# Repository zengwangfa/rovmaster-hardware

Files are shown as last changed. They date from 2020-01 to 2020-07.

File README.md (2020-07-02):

<div align="center">
  
  <a href="https://github.com/ROV-Master/rovmaster-hardware"><h1>ROV-Master</h2></a>
</div>

<div align="center">
  
  
  
</div>

## 1.ROV Master 硬件说明:pencil2:

> 电源供电为DC300V，主板基于NanoPi NEO Core，外部扩展PWM、ADC，采用电力载波/光纤与[地面站](https://github.com/ROV-Master/rovmaster-hardware)进行通信.

| 序号 | 文件夹名 | 用途 |
| :---: | :---: | :---: |
| 1 | [ROV Master Interface Board](https://github.com/ROV-Master/rovmaster-hardware/tree/master/1.ROV%20Master%20Interface%20Board%20%20V2.0) | 接线板，插入主板，用于给PWM设备信号线接入 |
| 2 | [ROV Master Mainboard](https://github.com/ROV-Master/rovmaster-hardware/tree/master/2.ROV%20Master%20Mainboard%20V3.0) | 主板，主控 |
| 3 | [ROV Master Powerboard](https://github.com/ROV-Master/rovmaster-hardware/tree/master/3.ROV%20Master%20%20Powerboard%20%20V1.0) | 舱内电源板，为设备提供1500W电源输出 |
| 4 | [ROV Master Ground Station](https://github.com/ROV-Master/rovmaster-hardware/tree/master/4.ROV%20Master%20Ground%20Station%20V1.0) | 地面站，提供通信转接及高压直流电源 |
| 5 | [ROV Master Zoom Controller](https://github.com/ROV-Master/rovmaster-hardware/tree/master/5.ROV%20Master%20Zoom%20Controller%20V3.0) | 变焦镜头控制板 |
| 6 | MP1584 VRM（Voltage Regulator Module） | 低压电源模块，4.5~28V输入，峰值3A，额定1.5A |
| 7 | [lib](https://github.com/ROV-Master/rovmaster-hardware/tree/master/lib) | Altium Designer 封装库 |

舱内装配图

## 2.ROV Master 硬件进展:family:

- [x] 舱内电路设计
	- [x] 接线板 by [@Ian](https://github.com/zengwangfa)
	- [x] ROV Master主板 by [@Ian](https://github.com/zengwangfa)	
	- [x] 舱内电源板 by [@Hyf](https://github.com/Hyf338)
- [x] 地面站 by [@Ian](https://github.com/zengwangfa)	

---

- [ ] 配件
	- [x] 变焦镜头控制板 by [@Ian](https://github.com/zengwangfa)	
	- [x] 深度传感器
		- [x] MS5837 I2C版本 by [@Ian](https://github.com/zengwangfa)	
		- [x] SPL1301 I2C版本 by [@Ian](https://github.com/zengwangfa)		 
	- [ ] MS5837 UART自带解算版本
	- [ ] 电调
		- [ ] 单向电调
		- [ ] 双向电调
	- [ ] 9轴模块
	- [ ] 水下监控摄像头
	- [ ] 探照灯
	- [ ] 舵机调试器	
	- [x] DC-DC 24V/3A 降压模块

#### Github下载过慢
- [Github下载过慢解决办法](https://blog.csdn.net/wangshuaiwsws95/article/details/104730741/)
	
#### 参与贡献
- Fork 本仓库
- 新建分支
- 提交
- 新建 Pull Request
- [点击联系我](Mailto:zengwangfa@outlook.com)

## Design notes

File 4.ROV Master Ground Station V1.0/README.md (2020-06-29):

<p align="center">
  
</p>

<p align="center">
  
  
</p>

# 1.新增加的特性

- 使用MT7688N模块，作为无线路由器(PC端网口、电力载波网口、光电转换网口、WiFi之间进行透传)
- 使用AC-DC隔离开关电源模块[Hi-Link 20W DC24V](https://detail.tmall.com/item.htm?id=607394173667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)对地面站设备进行供电，并在AC220V前端增加EMI滤波、保护电路
- 增加光电转换器接口
- 增加AC220电流电压表

地面站实物图

# 2.说明

- [仪表盒开孔尺寸图 文件夹](https://github.com/ROV-Master/rovmaster-hardware/tree/master/4.ROV Master Ground Station V1.0/仪表盒开孔尺寸图) 存放地面站**侧板**、上盖板开孔尺寸图

地面站内部设计连接图

# 3.后续可改进的地方
- 1.壳体上盖板电流电压表位置，开孔外扩0.5mm即可（原先为1mm）
- 2.WAN口可引出RJ45接口备用
- 3.PC端RJ45网口可挨紧

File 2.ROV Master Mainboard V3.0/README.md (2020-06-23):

<p align="center">
  
</p>

<p align="center">
  
  
</p>

# 1.新增加的特性

- 增加PWM端光耦隔离
- 电源输入为高压直流输入(DC300V)
- 稳压电源后端3.3V、5.0V增加TVS管(在稳压模块异常时保护后端电路)

# 2.说明

- `MainBoard.step`文件为PCB 3D视图文件
- `电源接口及电流采样`文件夹为之前原理图备份

# 3.后续可改进的地方

- 放置请勿触摸图标
- 增加DC310V测试点
- 蜂鸣器`BEEP(C0)`引脚加一个1K下拉引脚
- 地之间隔离的磁珠可以并联一个103电容(用于吸收杂波)
- TVS管标称电压(VRWM)应略大于工作电压，TVS的钳制电压(VCL)尽量大

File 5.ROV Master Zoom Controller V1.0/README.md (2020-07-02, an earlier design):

<p align="center">
  
</p>

<p align="center">
  
  
</p>

# 1.新增加的特性

- 使用`MCU` STM32F103C8T6 
- 增加`CP2102`  USB转UART模块进行调试
- 使用A4988步进电机驱动模块

# 2.说明

[A4988 文件夹](https://github.com/ROV-Master/rovmaster-hardware/tree/master/5.ROV Master Zoom Controller V1.0/A4899) 存放A4988步进电机驱动芯片datasheet、尺寸图

# 3.后续改进的地方

### 3.1 设计缺陷
- A4988驱动器为驱动8~35V步进电机，若为低压步进电机可以使用[DRV8834驱动模块](https://www.pololu.com/product/2134) 

A4988步进电机励磁序列

变焦镜头步进电机励磁序列

| STEP |  1 |  22  |  33  |  4 |
| :--: | :--: | :--: | :--: | :--: |
|  A+  |  1 |  1 |  0 |  0 |
|  A-  |  1 |  0 |  0 |  1 |
|  B+  |  0 |  0 |  1 |  1 |
|  B-  |  0 |  1 |  1 |  0 |

- 由上图可知，但是由于变焦镜头步进电机节拍表与普通的并不一致，因此此类型的驱动模块并不适用

### 3.2 解决方案
- 因而需要使用最原有方案，利用达林顿管芯片进行驱动(eg.ULN2803、ULN2003驱动芯片)
- ULN2003为7通道达林顿管，但是变焦镜头有2个4相步进电机，因此使用ULN2803驱动芯片（8通道）

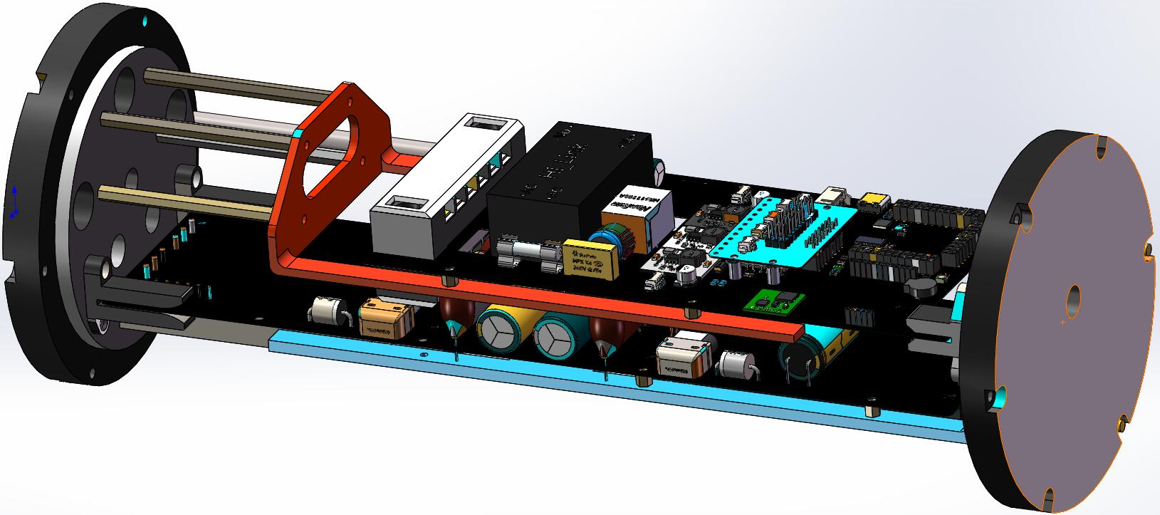
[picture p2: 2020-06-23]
doc/pictures/Chamber_structure1.jpg

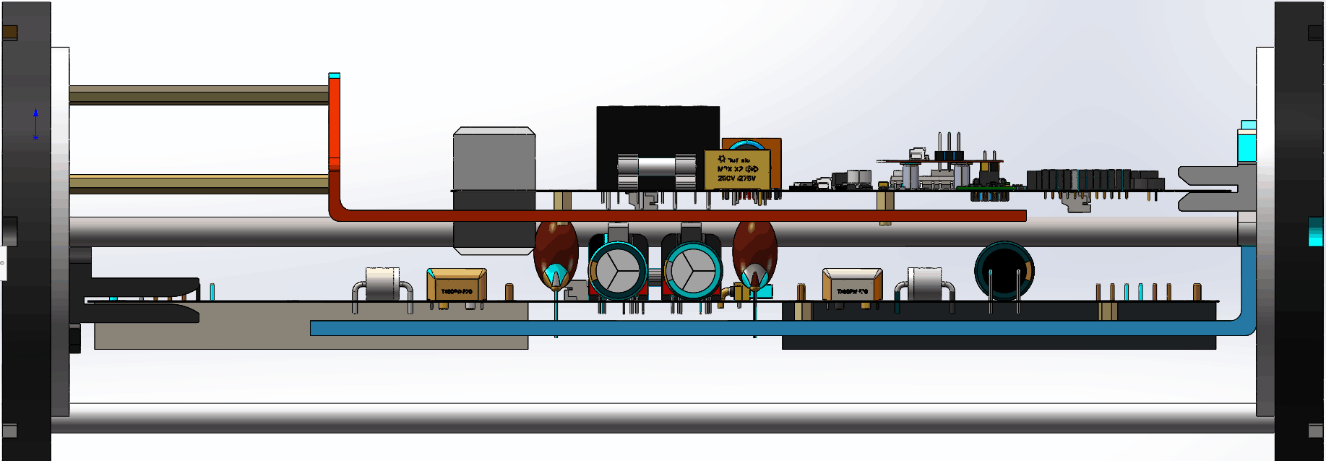
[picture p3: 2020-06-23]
doc/pictures/Chamber_structure2.png

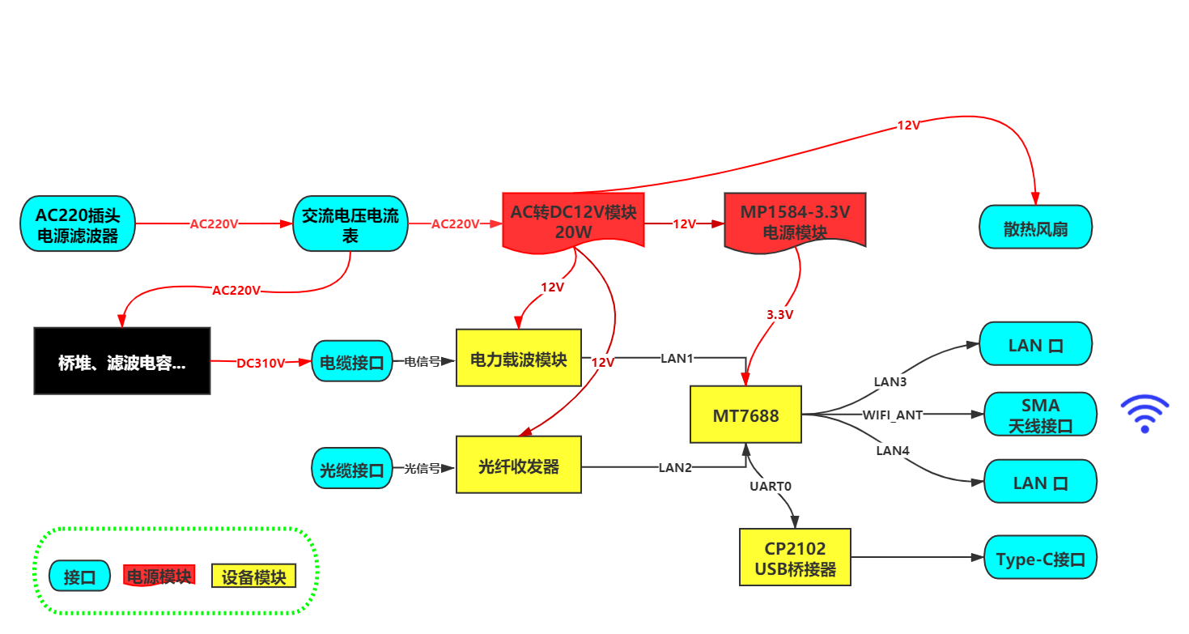
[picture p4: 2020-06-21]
4.ROV Master Ground Station V1.0/Ground_Station_Structrue.png

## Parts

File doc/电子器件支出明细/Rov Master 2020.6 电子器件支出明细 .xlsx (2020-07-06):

ROV 电子器件支出明细表
器材名称 | 数量 | 总价 | 日期 | 是否有发票
捷配 第一代主板PCB | 5 | 108 |  | 1电子发票
220V转24V20W稳压隔离电源模块 (https://detail.tmall.com/item.htm?id=607394173667&_u=k1v2ldgsf448&skuId=4432714442007) | 4 | 94 | 6.11 | 电子发票
PCB板清洗剂除胶除尘 (https://item.taobao.com/item.htm?spm=a1z09.2.0.0.2d1f2e8do3zeDh&id=9893313086&_u=k1v2ldgsa688) | 1 | 17 | 6.12
大功率二极管30A10单向导通 (https://item.taobao.com/item.htm?spm=a1z09.2.0.0.2d1f2e8do3zeDh&id=581965527987&_u=k1v2ldgse40c) | 10 | 21.8 | 6.12
定制XT60/XT30电源线 (https://detail.tmall.com/item.htm?id=15100319583&spm=a1z09.2.0.0.2d1f2e8do3zeDh&_u=k1v2ldgs5d34) | 10/5 | 180 | 6.13 | 1
TB1506接线端子/6位短路片 (https://detail.tmall.com/item.htm?id=610080819934&spm=a1z09.2.0.0.2d1f2e8do3zeDh&_u=k1v2ldgsf44b) | 10 | 32.79 | 6.13
XT30接头/电源硅胶线 (https://detail.tmall.com/item.htm?id=559203984858&spm=a1z09.2.0.0.2d1f2e8do3zeDh&_u=k1v2ldgscda4) | 5 | 36.65 | 6.13
芯片主板元器件散热片 (https://item.taobao.com/item.htm?spm=a1z09.2.0.0.2d1f2e8do3zeDh&id=602118161849&_u=k1v2ldgsba53) | 5 | 7.1 | 6.13
捷配 主板/电源板PCB (https://detail.tmall.com/item.htm?id=597612948368&spm=a1z09.2.0.0.2d1f2e8do3zeDh&_u=k1v2ldgsaa5d) | 5/5 | 324 | 6.13 | 1电子发票
PCA9685芯片 (https://item.taobao.com/item.htm?spm=a1z09.2.0.0.2d1f2e8do3zeDh&id=557114520914&_u=k1v2ldgs5378) | 4 | 25.87 | 6.14
JY901B 九轴模块 (https://item.taobao.com/item.htm?spm=a1z09.2.0.0.2d1f2e8do3zeDh&id=43511899945&_u=k1v2ldgsb9b2) | 1 | 134 | 6.14 | 1
塑料盒长方形盒子工具盒 (https://detail.tmall.com/item.htm?id=581874651313&spm=a1z09.2.0.0.2d1f2e8do3zeDh&_u=k1v2ldgs4223) | 1 | 71.88 | 6.14 | 1电子发票
优信 电子元器件 (https://youxin-electronic.taobao.com/shop/view_shop.htm?user_number_id=2658592015) | 若干 | 171.8 | 6.14 | 1
贴片单排母/排针 (https://detail.tmall.com/item.htm?id=569406041078&spm=a1z09.2.0.0.2d1f2e8do3zeDh&_u=k1v2ldgs0d14) | 5 | 12.8 | 6.14
元器件收纳盒 (https://item.taobao.com/item.htm?spm=a1z09.2.0.0.2d1f2e8do3zeDh&id=43331772336&_u=k1v2ldgs6af2) | 3 | 58.82 | 6.14
220V 交流电压电流表/热缩管 (https://item.taobao.com/item.htm?spm=a1z09.2.0.0.300e2e8dPqPSZj&id=563971657103&_u=n1v2ldgsf55d) | 1/3 | 124.35 | 6.20 | 1
插座式紧凑型电源滤波器 (https://item.taobao.com/item.htm?spm=a1z09.2.0.0.300e2e8dPqPSZj&id=607137400635&_u=n1v2ldgs7cbf) | 2 | 101 | 6.20 | 1
MT7688路由器模块/稳压隔离电源 (https://detail.tmall.com/item.htm?id=597619548455&spm=a1z09.2.0.0.300e2e8dPqPSZj&_u=n1v2ldgs2484) | 2/2 | 153 | 6.20 | 1电子发票
荣新 地面站PCB/侧板PCB/侧板PCB (https://item.taobao.com/item.htm?spm=a1z09.2.0.0.300e2e8dPqPSZj&id=9379760689&_u=n1v2ldgs2b09) | 5/5/5 | 271 | 6.21 | 1电子发票
优信 电子元器件 (https://youxin-electronic.taobao.com/shop/view_shop.htm?user_number_id=2658592015) | 若干 | 221.3 | 6.21 | 1
贴片单排母/排针 (https://detail.tmall.com/item.htm?id=569406041078&spm=a1z09.2.0.0.2d1f2e8do3zeDh&_u=k1v2ldgs0d14) | 若干 | 39.8 | 6.23 | 1电子发票
A4988步进电机模块 (https://detail.tmall.com/item.htm?id=610688807041&spm=a1z09.2.0.0.300e2e8deJ7bMh&_u=n1v2ldgs5d2d) | 2 | 9.6 | 6.23
冷压插头接线端子公母快速连接器 (https://detail.tmall.com/item.htm?id=620331380782&spm=a1z09.2.0.0.977a2e8dSL2XP5&_u=t1v2ldgs7800) | 50 | 13.34 | 6.24
双头USB口数据线两头公对公 (https://buyertrade.taobao.com/trade/detail/tradeSnap.htm?tradeID=1085822114156724883&snapShot=true) | 3 | 41.53 | 6.25
全新静音风扇 2510 2.5厘米 12V (https://item.taobao.com/item.htm?spm=a1z09.2.0.0.977a2e8dSL2XP5&id=41680128557&_u=t1v2ldgs8321) | 3 | 25 | 6.27
20 AWG特软高温硅胶排线 (https://item.taobao.com/item.htm?spm=a1z09.2.0.0.977a2e8dSL2XP5&id=557843049825&_u=t1v2ldgs893e) | 3 | 22.2 | 6.27
优信 电子元器件 (https://youxin-electronic.taobao.com/shop/view_shop.htm?user_number_id=2658592015) | 若干 | 75 | 6.27 | 1
金属电缆防水接头葛兰头 (https://item.taobao.com/item.htm?spm=a1z09.2.0.0.977a2e8dSL2XP5&id=611336897072&_u=t1v2ldgsbf57) | 4 | 21.31 | 6.27
PH红白排线双头PH2.0mm端子线 (https://item.taobao.com/item.htm?spm=a1z09.2.0.0.977a2e8dSL2XP5&id=584930779544&_u=t1v2ldgs0031) | 30 | 45.4 | 6.29
优信 电子元器件 (https://youxin-electronic.taobao.com/shop/view_shop.htm?user_number_id=2658592015) | 若干 | 94.88 | 6.29 | 1
ULN2803 达林顿管 (https://detail.tmall.com/item.htm?id=41272630297&spm=a1z09.2.0.0.30552e8da7n1VT&_u=21v2ldgsc303) | 8 | 28.4 | 7.1
共计 |  | 2352.34

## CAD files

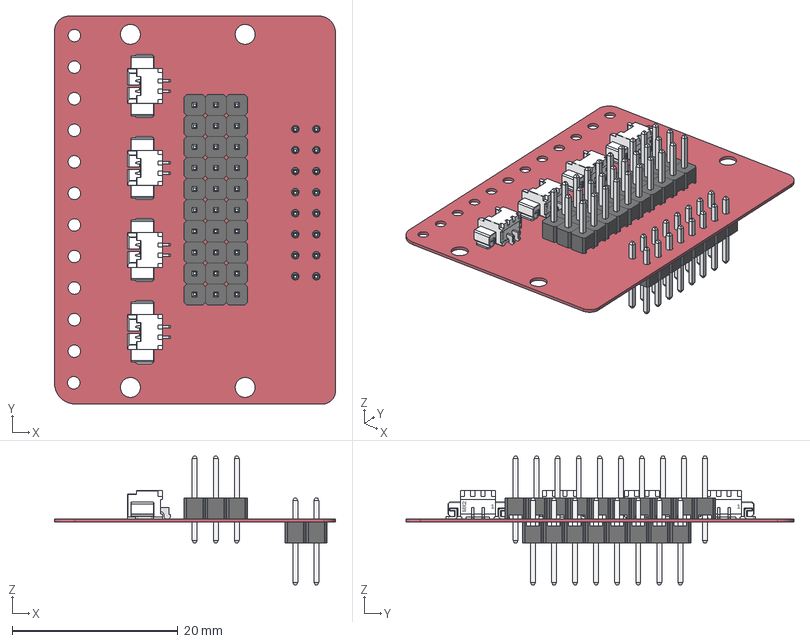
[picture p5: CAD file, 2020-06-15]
1.ROV Master Interface Board V2.0/interface.step
33.9 x 46.8 x 15.6 mm
Board
MOLEX1.25-WS-竘褐 x 8
LOGO?0.25 x 4
MOLEX1.25-WS-2P x 4
HEADER x 49

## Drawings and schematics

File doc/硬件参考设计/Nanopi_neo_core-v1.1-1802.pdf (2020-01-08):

# NanoPi NEO Core

# Revision

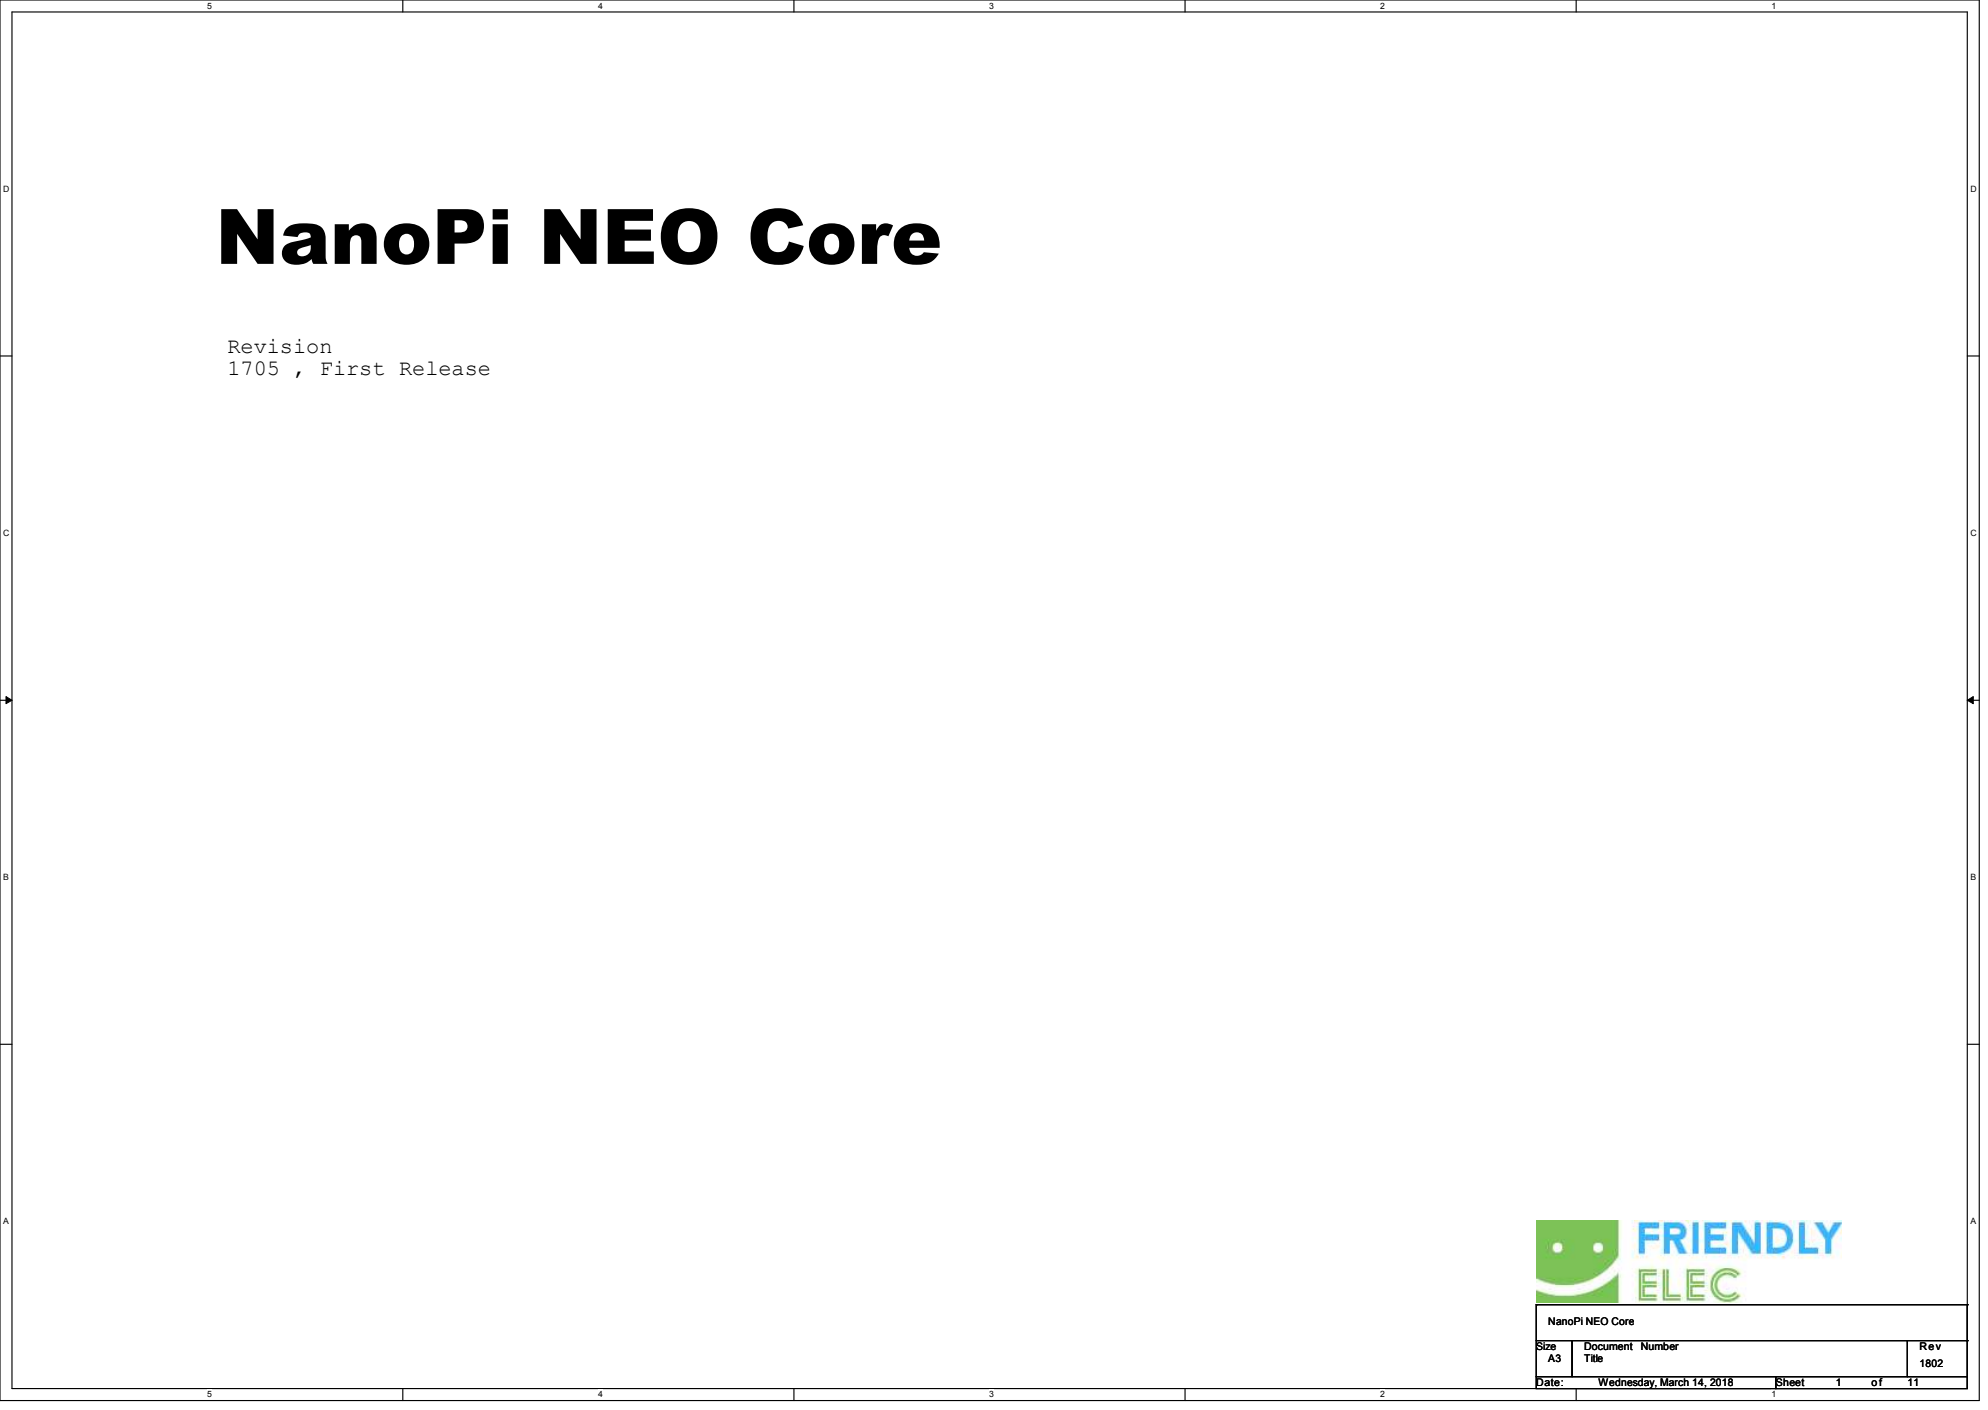
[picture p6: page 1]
1705 , First Release; Size; Document Number; Date:; Sheet; Title; Wednesday, March 14, 2018

NanoPi NEO Core

# BLOCK

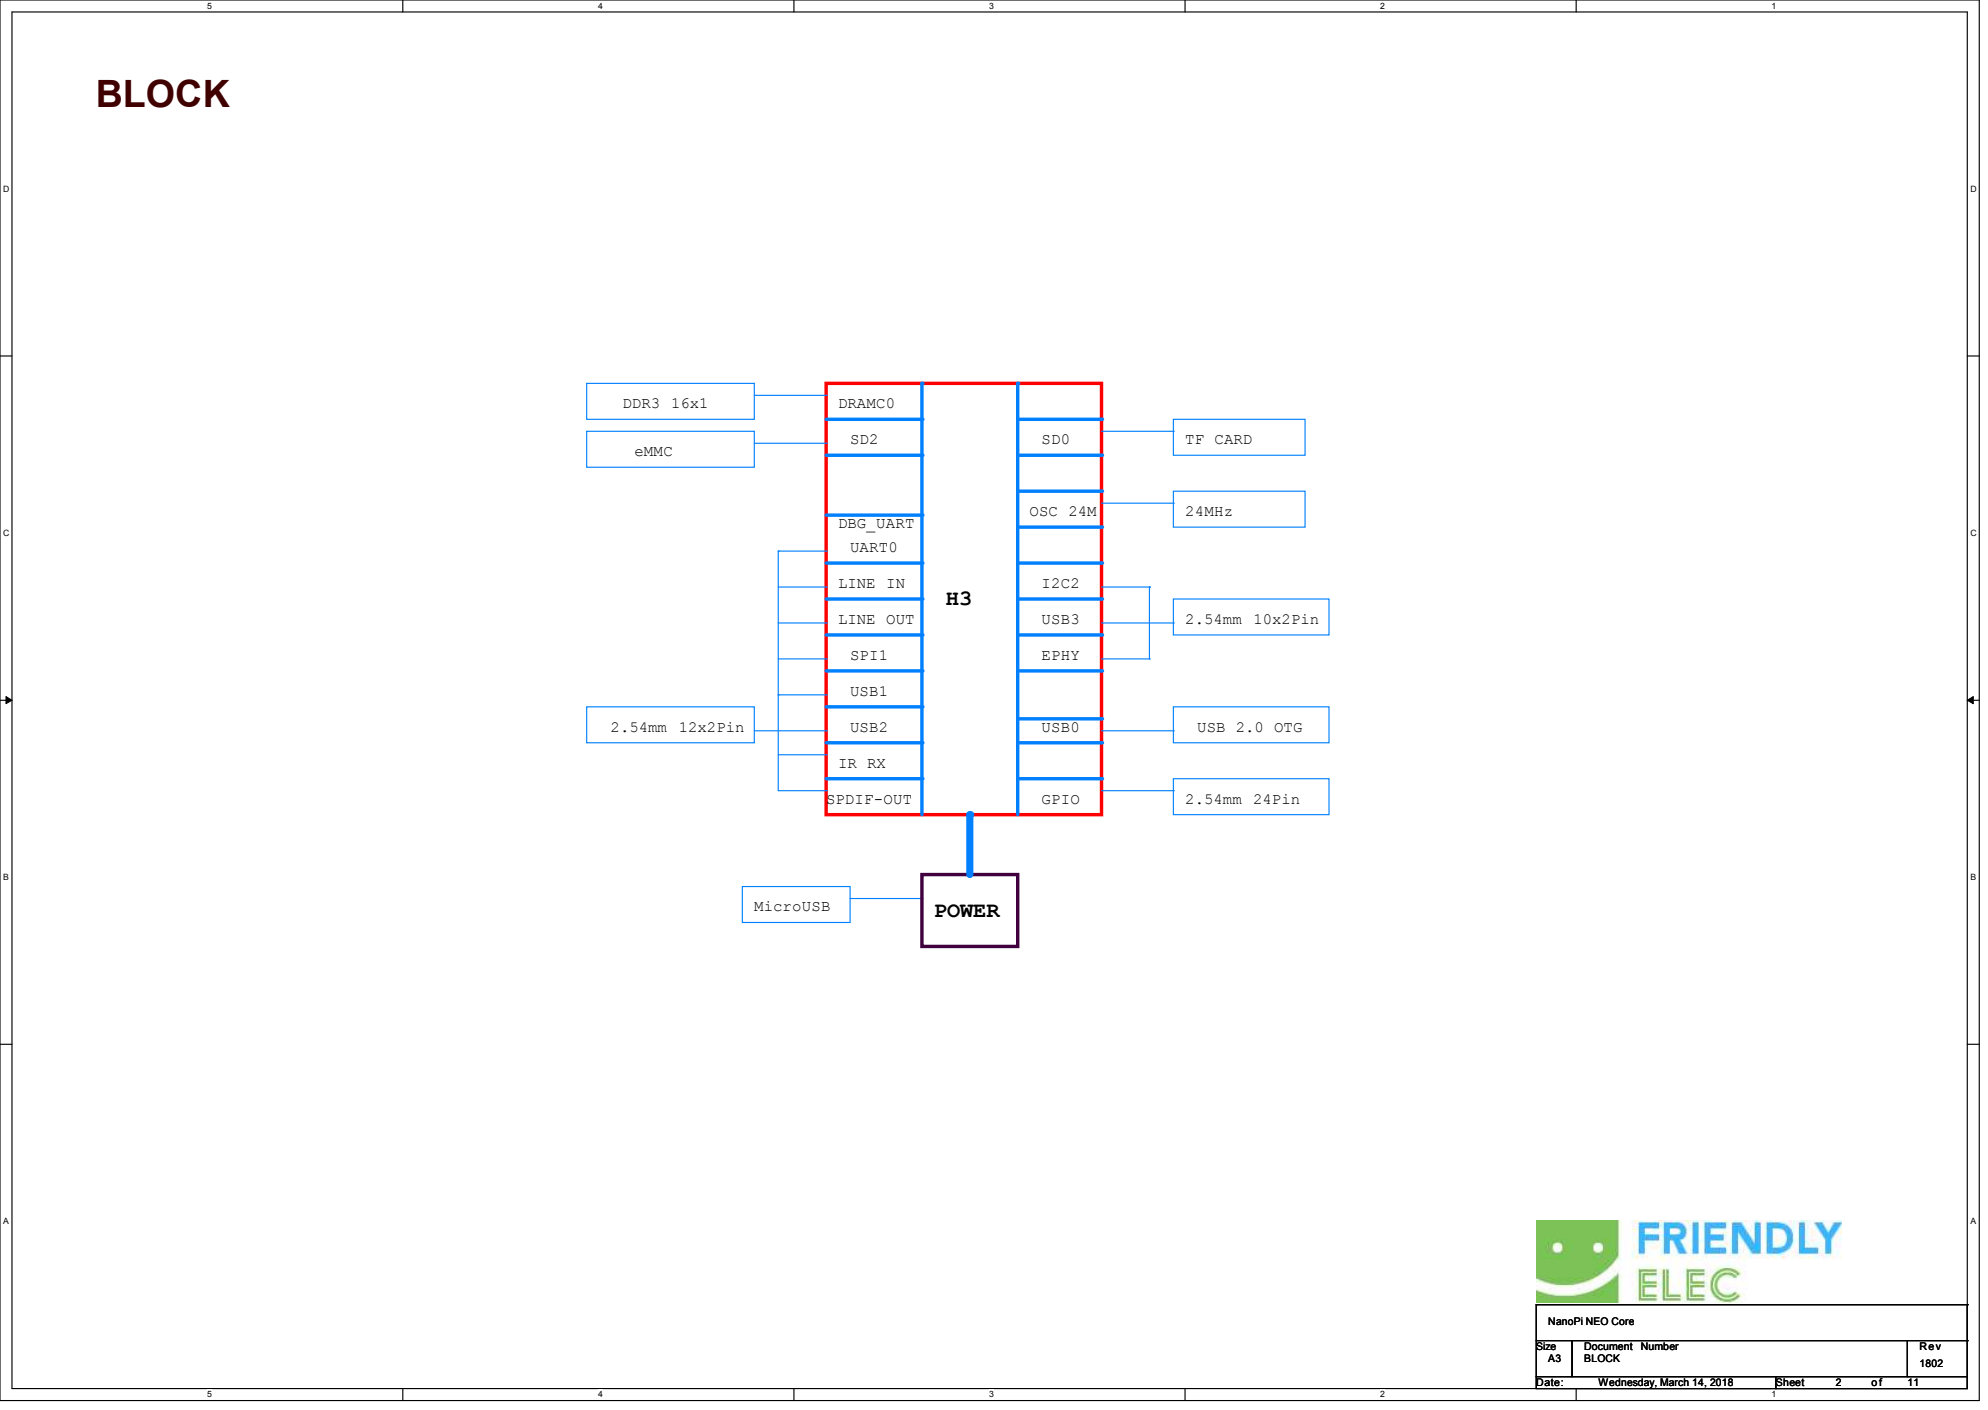
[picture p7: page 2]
TF CARD; USB0; USB1; OSC 24M; 24MHz; EPHY; MicroUSB; DDR3 16x1; DRAMC0; USB3; POWER; LINE OUT; 2.54mm 12x2Pin; USB2; USB 2.0 OTG; LINE IN; SPDIF-OUT; GPIO; 2.54mm 24Pin; UART0; DBG_UART; 2.54mm 10x2Pin; SPI1; SD2 eMMC; BLOCK; Wednesday, March 14, 2018

# POWER TREE

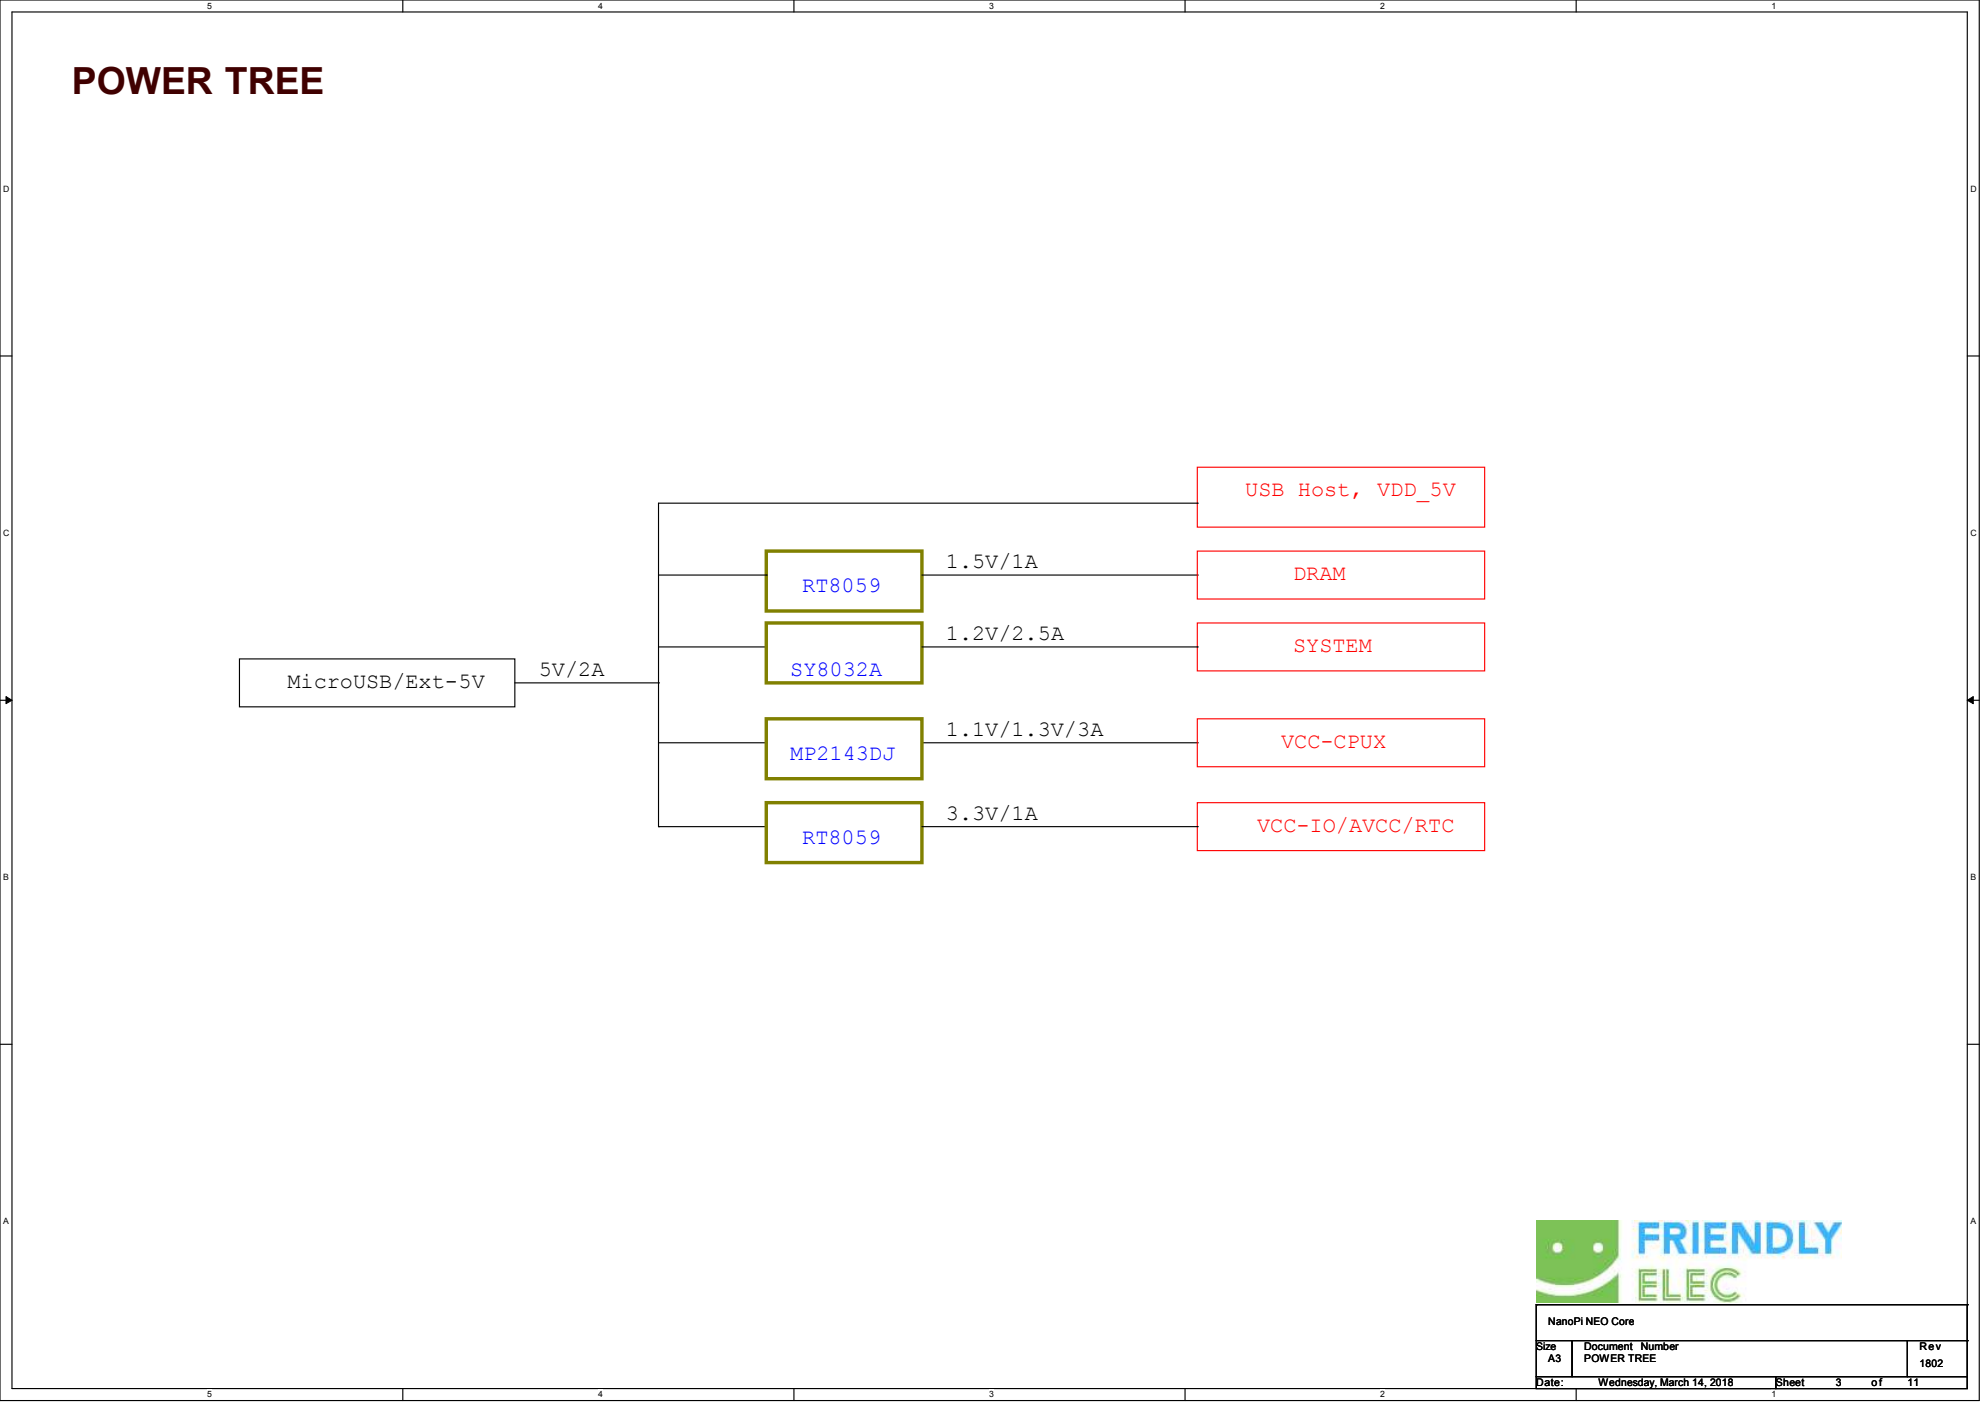
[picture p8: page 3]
MicroUSB/Ext-5V; USB Host, VDD_5V; DRAM; VCC-CPUX; SYSTEM 1.2V/2.5A; POWER TREE; Wednesday, March 14, 2018

VCC-IO/AVCC/RTC RT8059

# DDR3 16x1

# DRAM

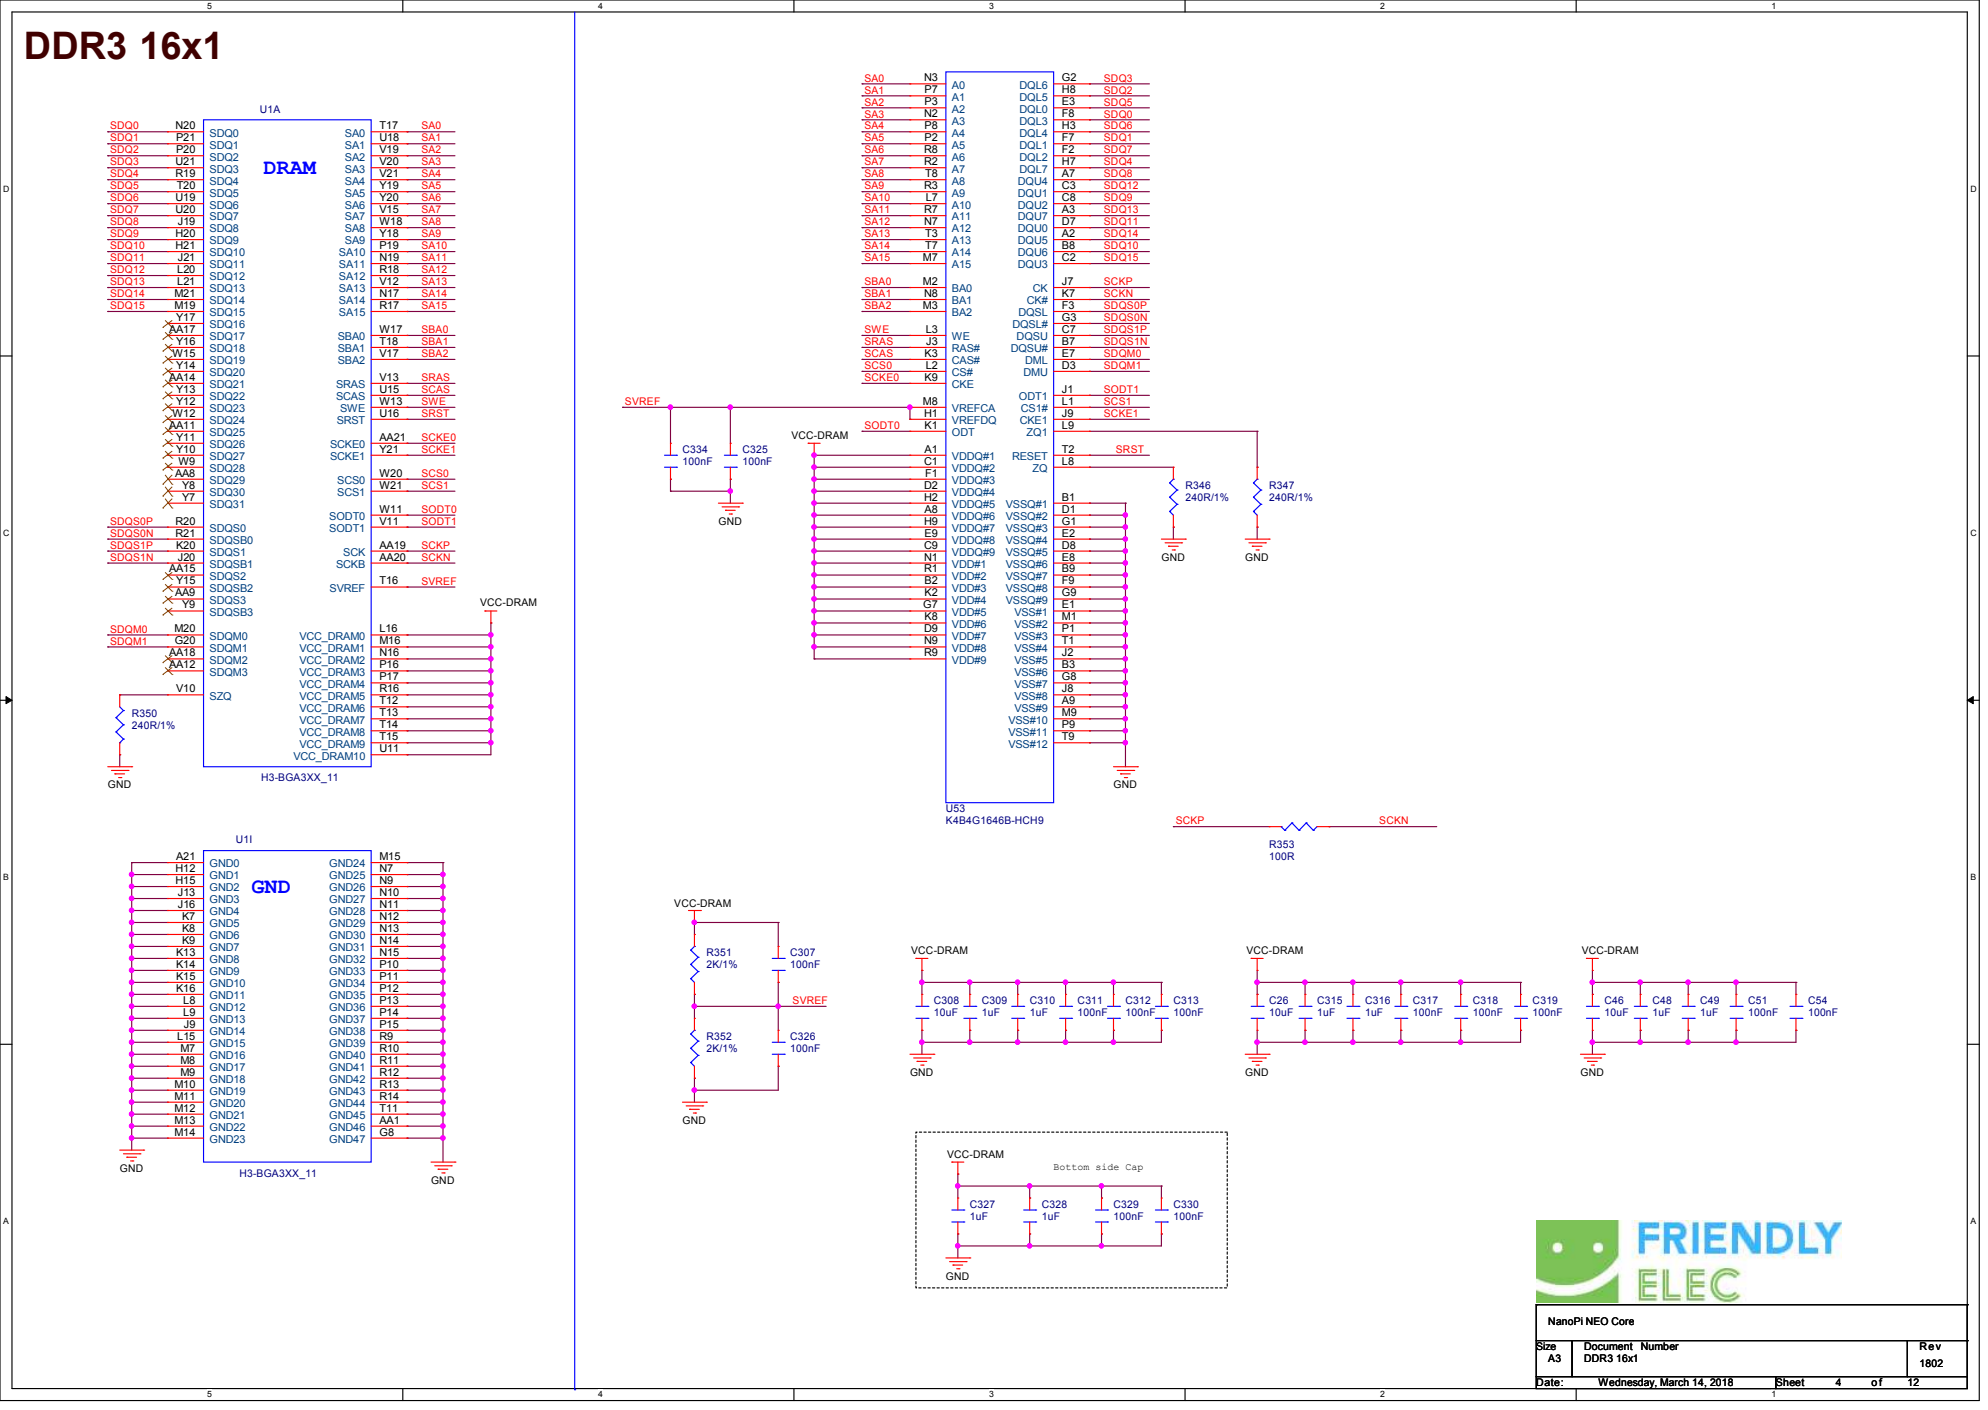
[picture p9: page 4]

# CPU 01

# SDC1

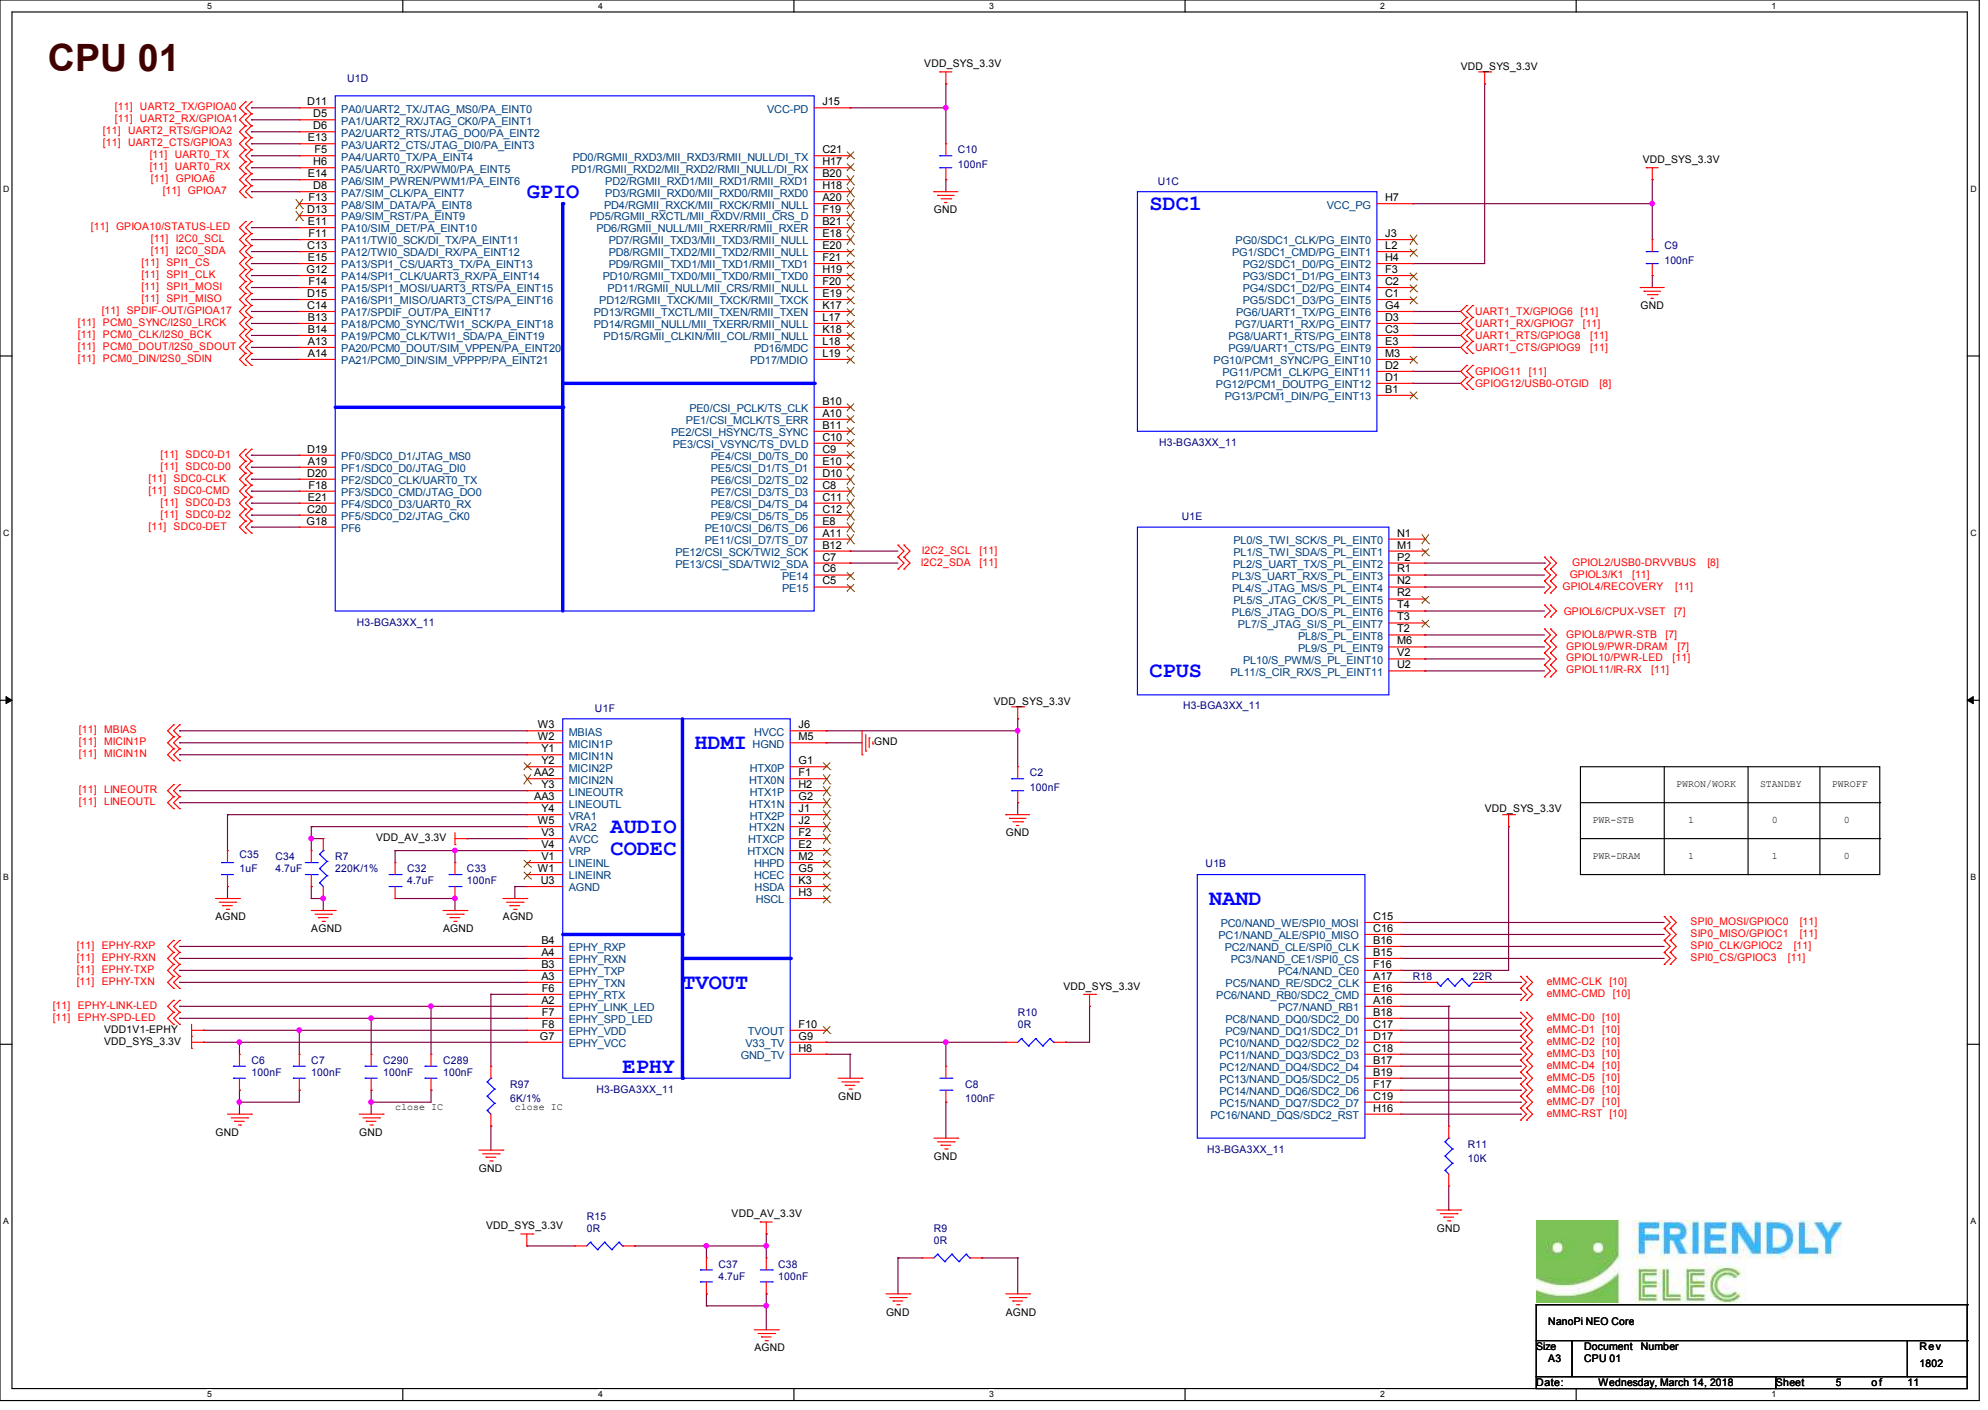
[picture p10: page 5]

# CPU 02

# USB

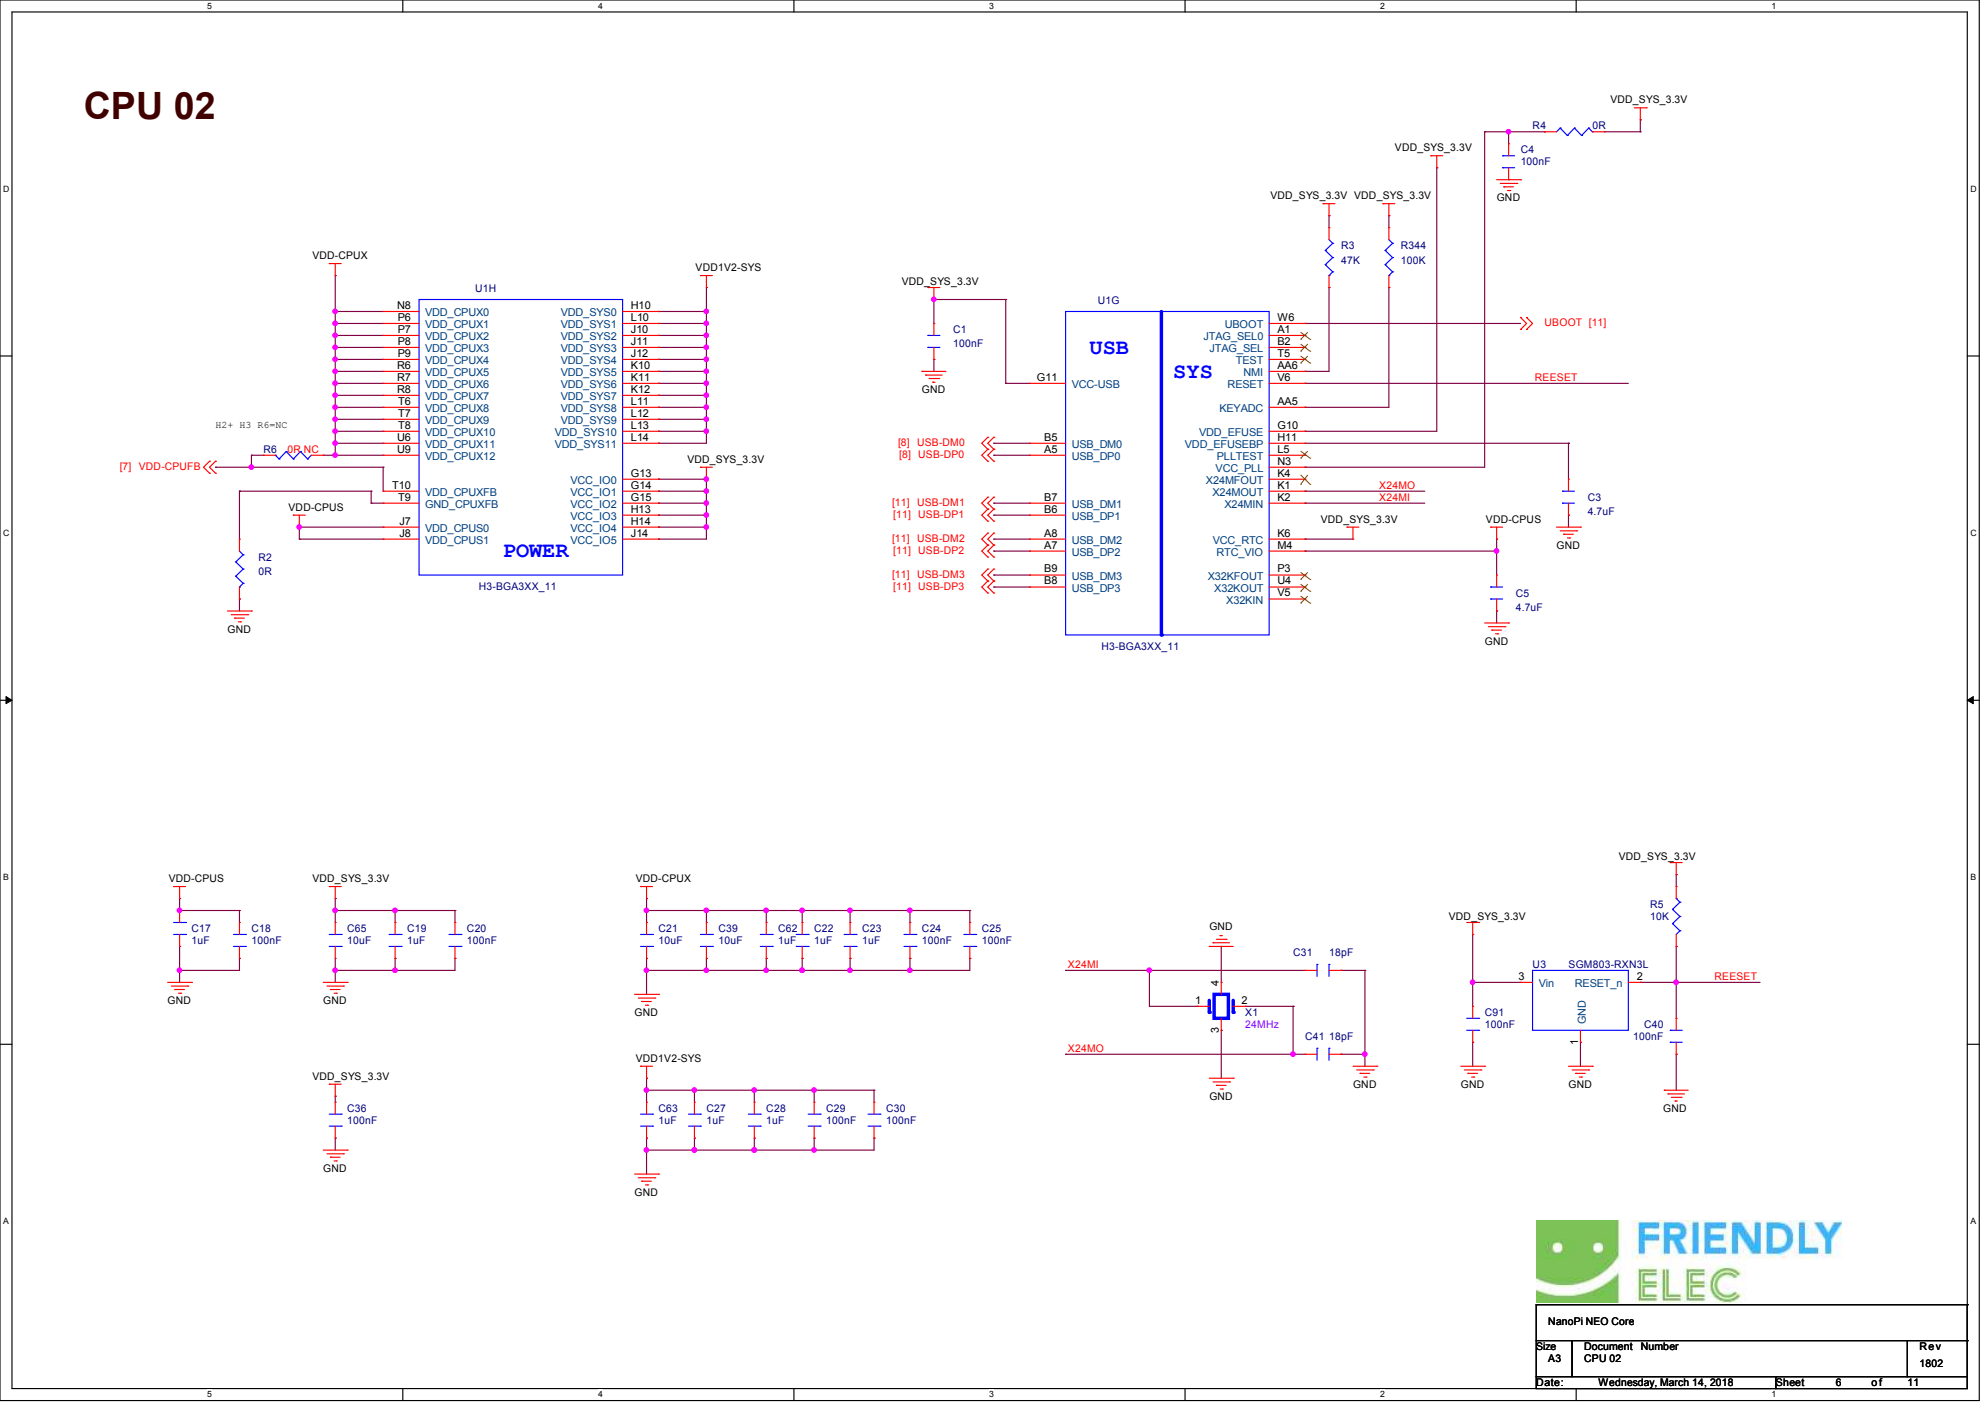
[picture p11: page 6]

# POWER 01

1.5V/1A

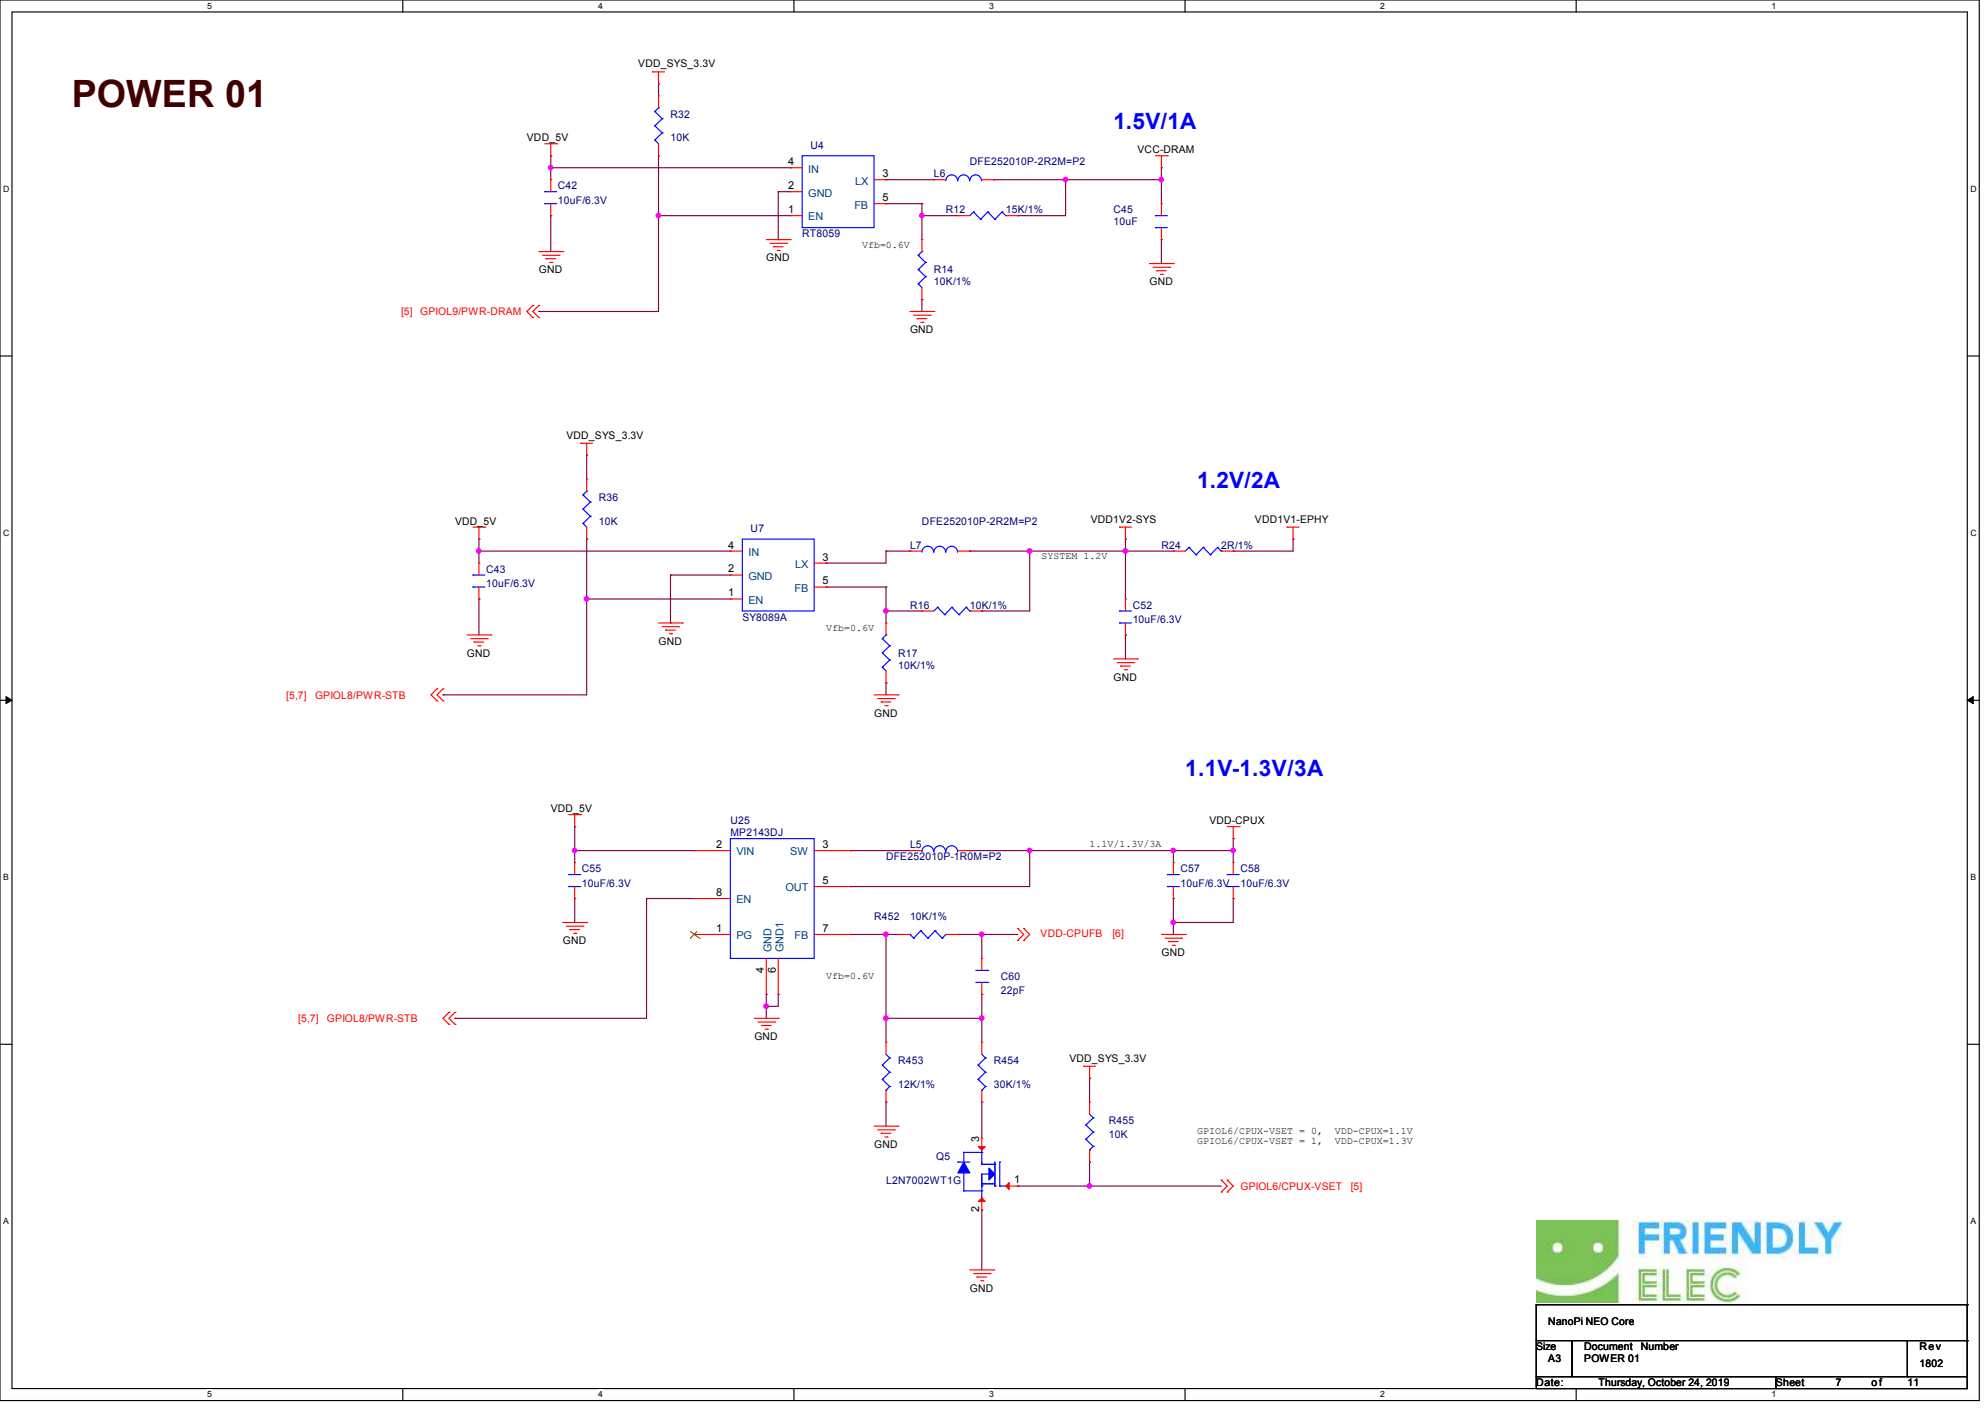
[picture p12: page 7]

D | D

# POWER 02

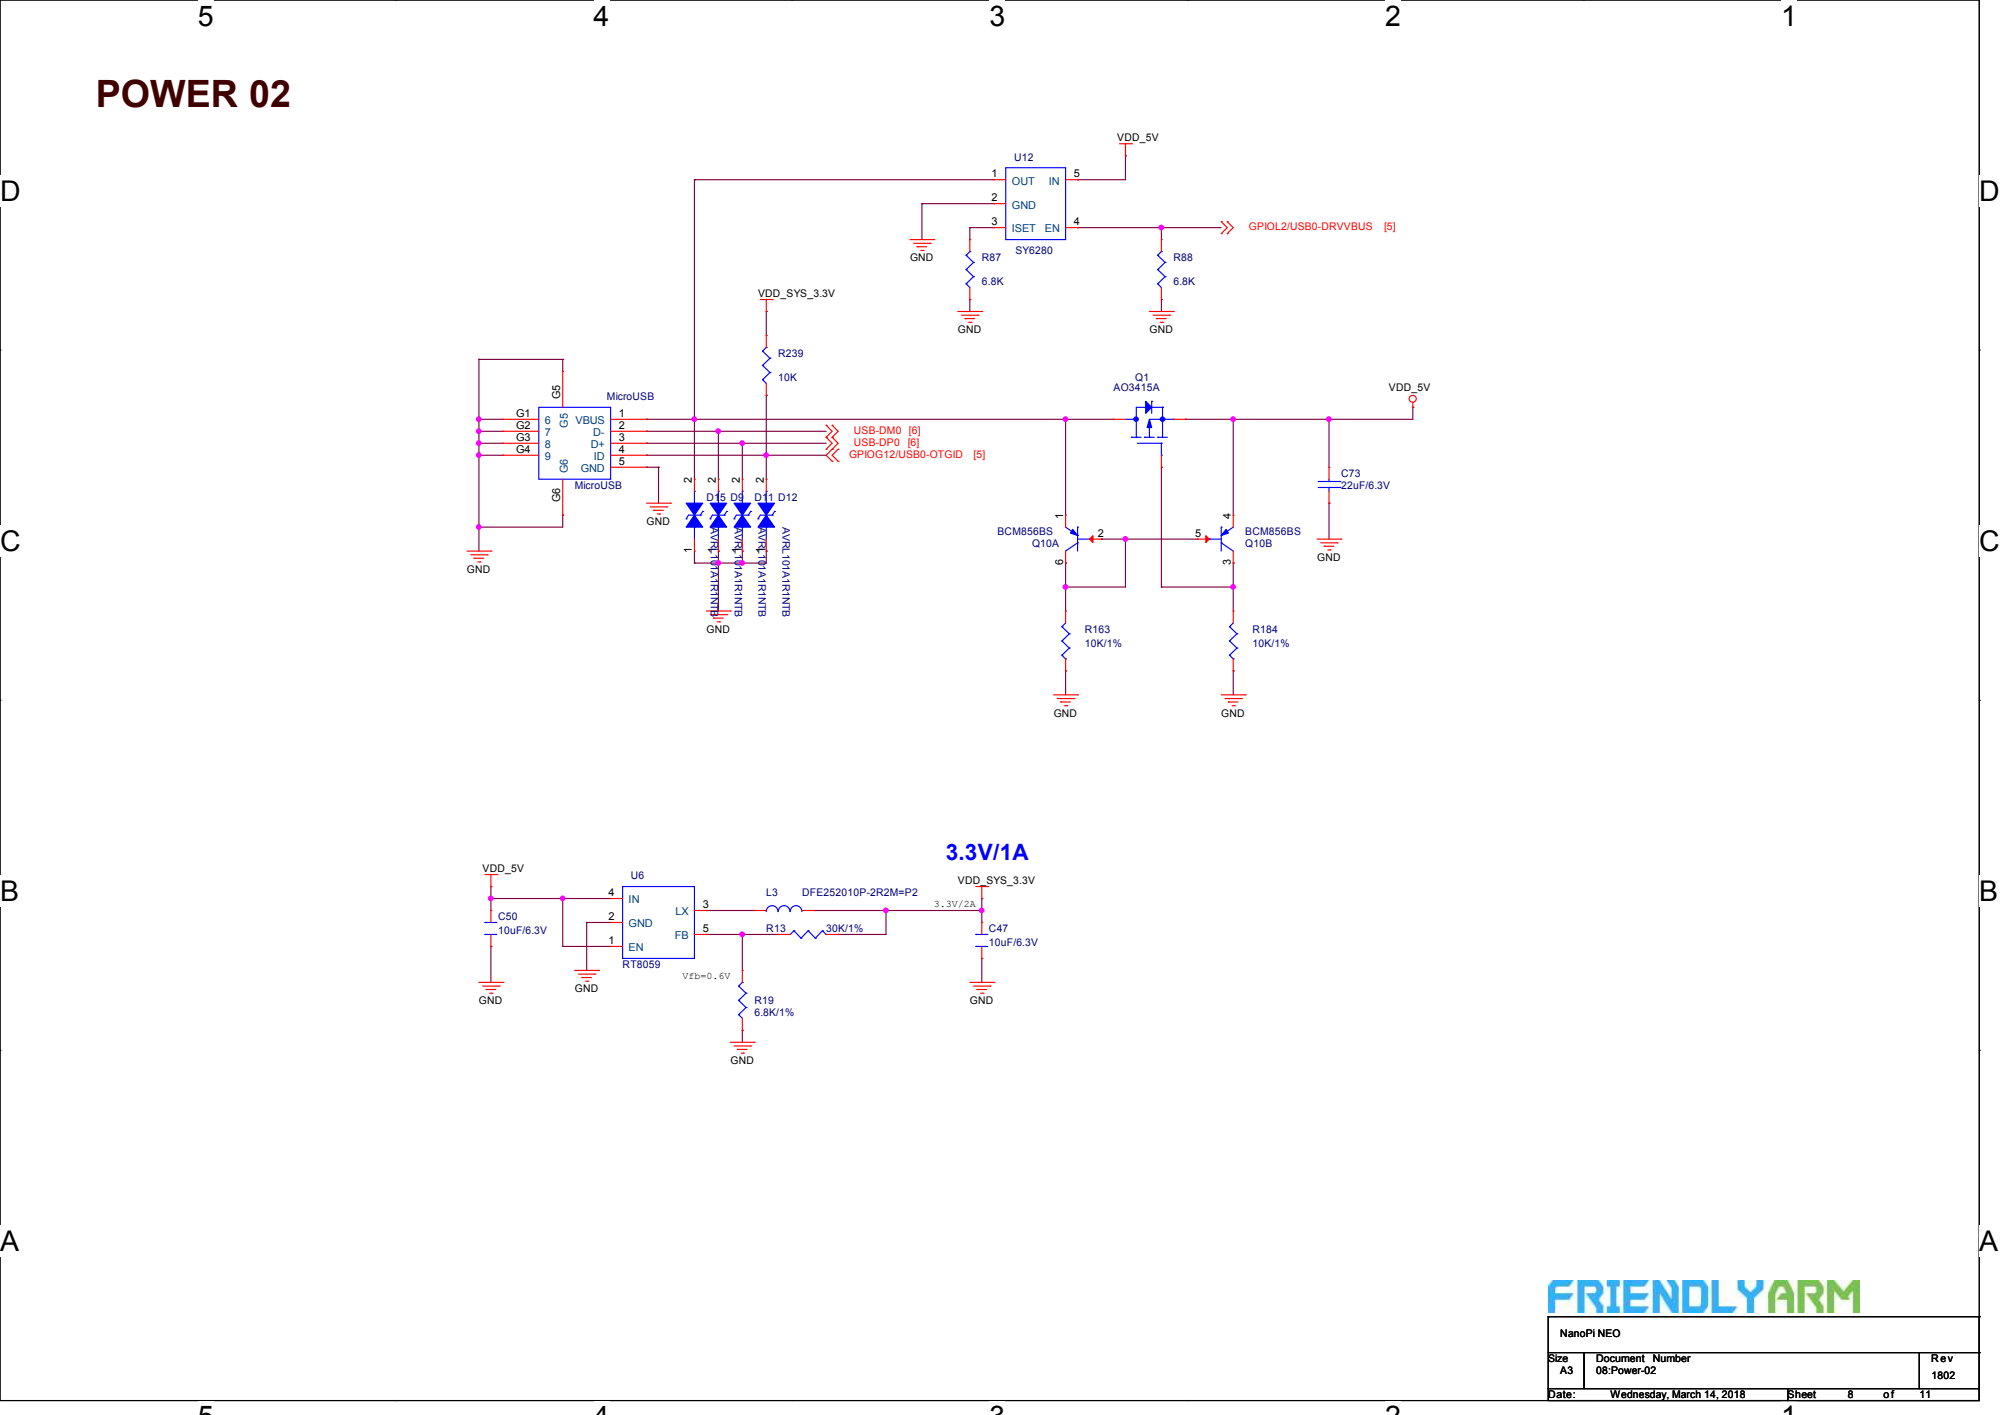
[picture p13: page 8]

# eMMC

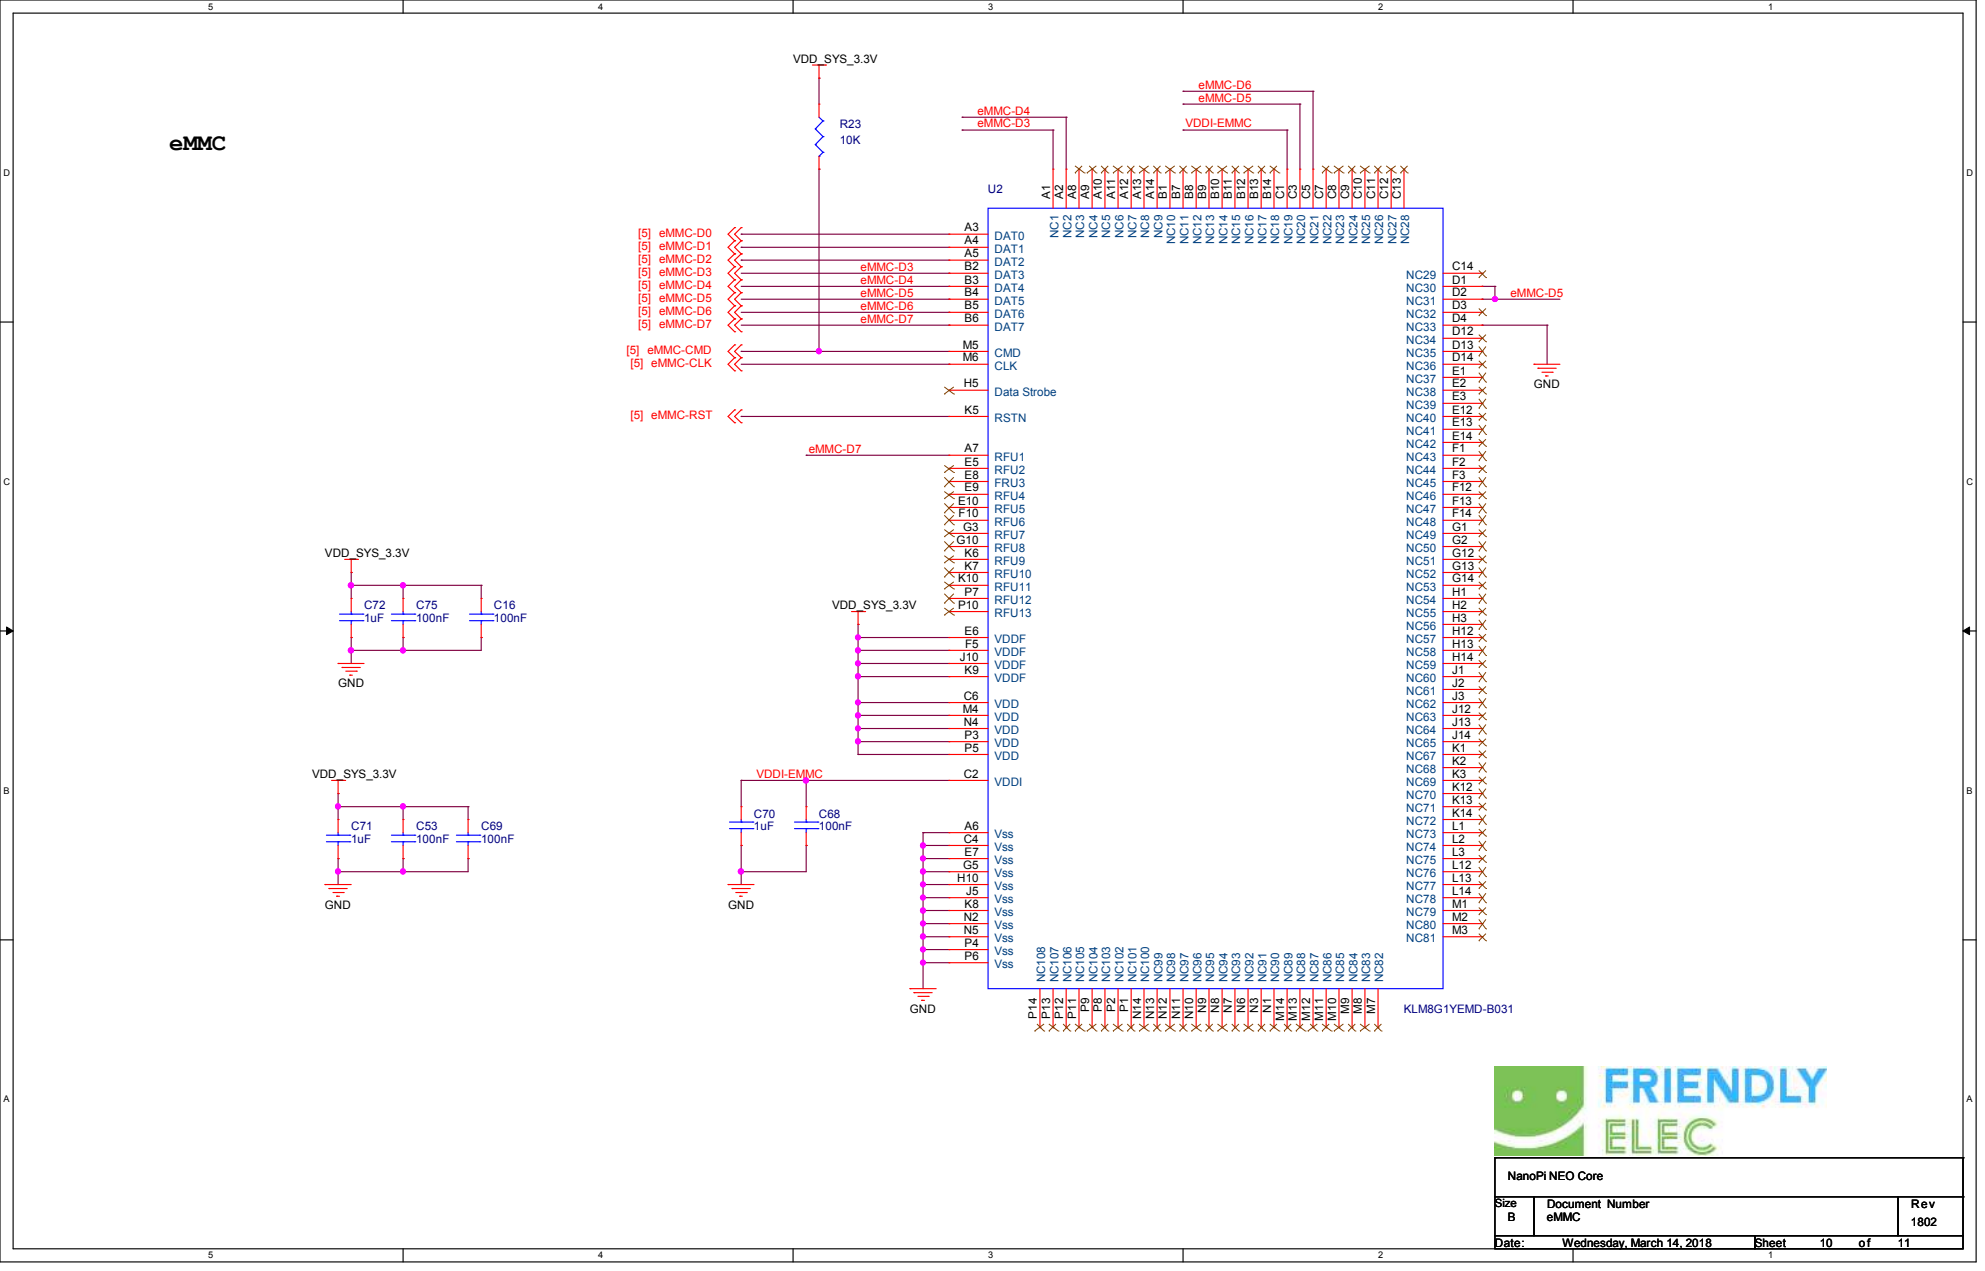
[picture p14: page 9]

# GPIO,Card,LEDs

## D4RClamp0531T/NC

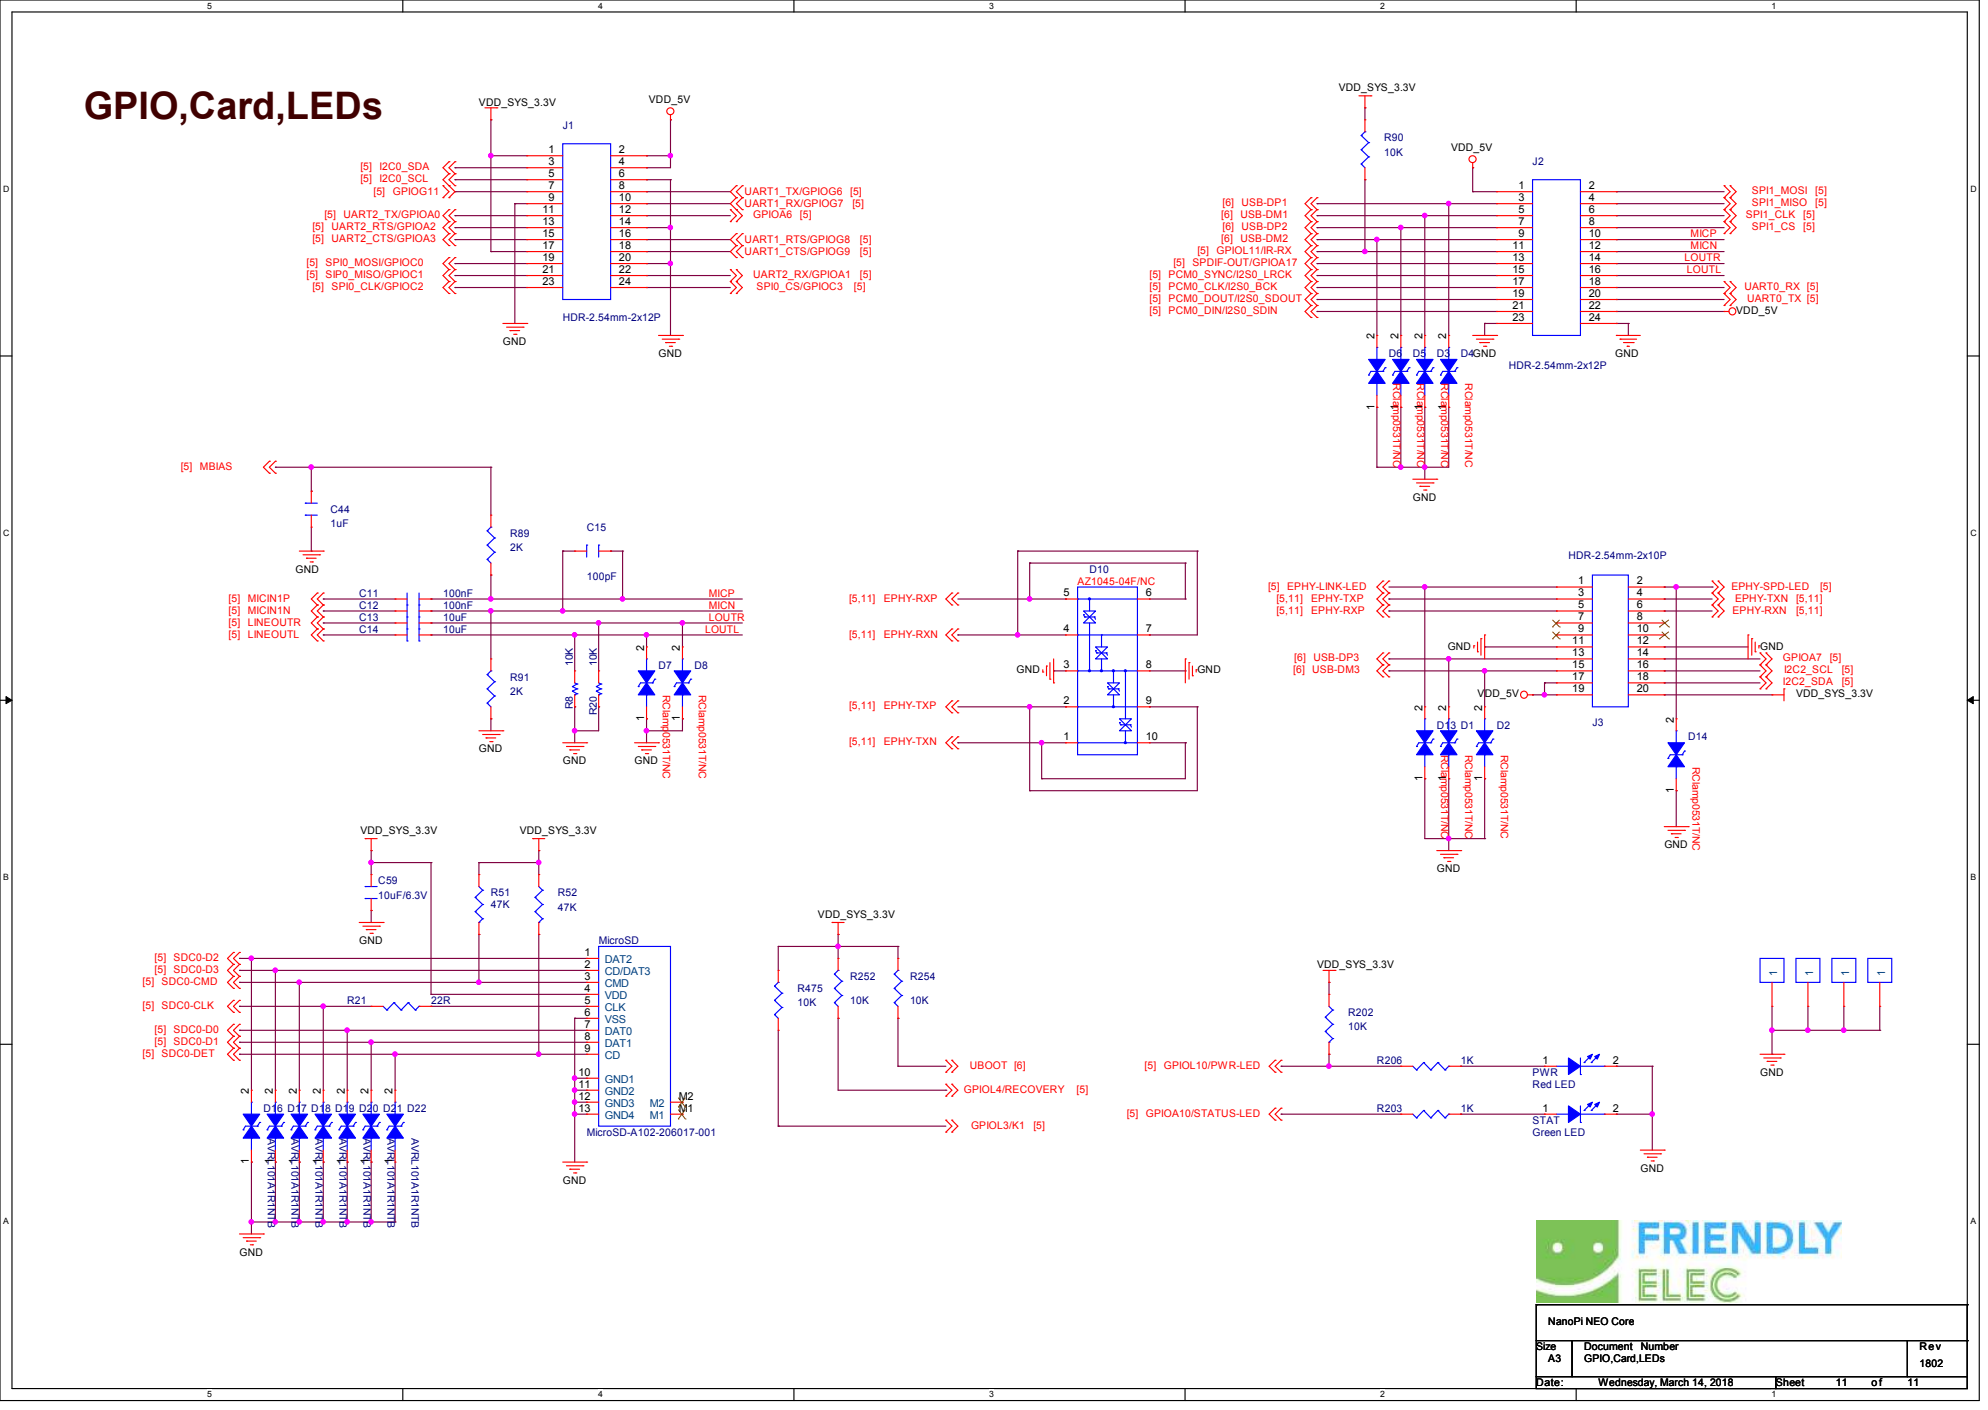
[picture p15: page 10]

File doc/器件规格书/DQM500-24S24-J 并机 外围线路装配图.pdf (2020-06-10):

一、 组装准备：

1、 将 2 只全砖模块铝板上粘贴的保护膜（黄色）全部揭掉。

2、 把模块铝板底部涂上导热硅脂，按照 S9A 型机壳内全砖位置用螺钉固定好。

3、 按端子位置把端子固定在前面板上，并把前面板上好。同时把+Vin、-Vin、+Vo、-Vo 用插针两两连好。

二、 接线说明：

1、 按下页图所示分别接线。输入正、负线各用 2 根 6 平方线，输出正负线各用 2 根 4 平方线。±S 线、PC 线

用 0.1 平方线。

2、 输入部分接好线后，用黄压敏绞带包绕好，以利绝缘。

3、 所有接线尽量最近、最短，输出线最好双绞。

4、 所有元件尽量焊低，不可超过机壳高度。

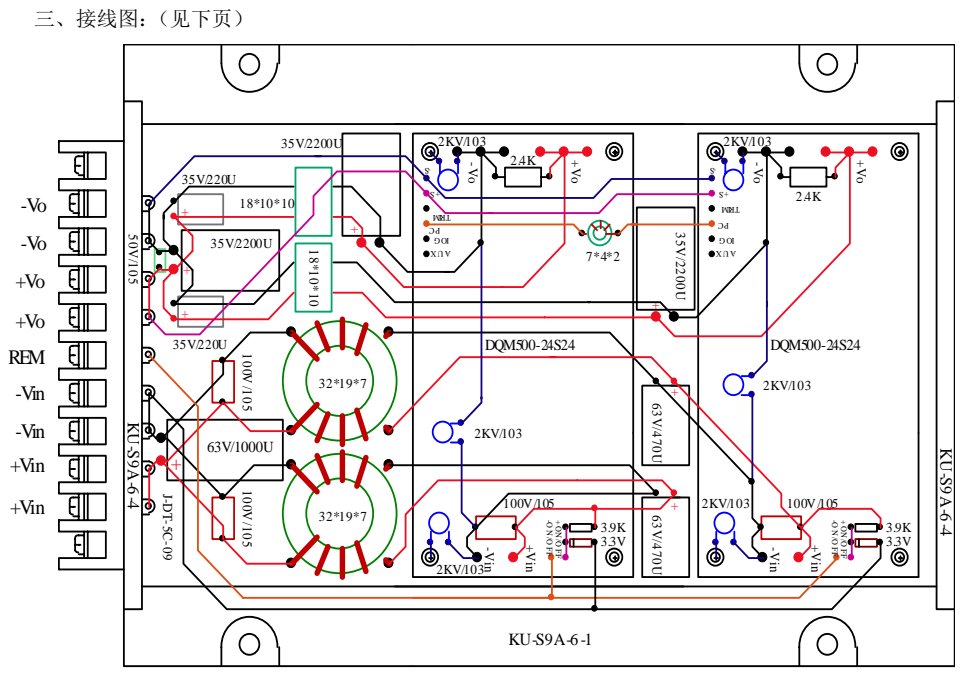
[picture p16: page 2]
三、接线图：（见下页）; -Vin; +Vin; DQM500-24S24; REM; -Vin +Vin

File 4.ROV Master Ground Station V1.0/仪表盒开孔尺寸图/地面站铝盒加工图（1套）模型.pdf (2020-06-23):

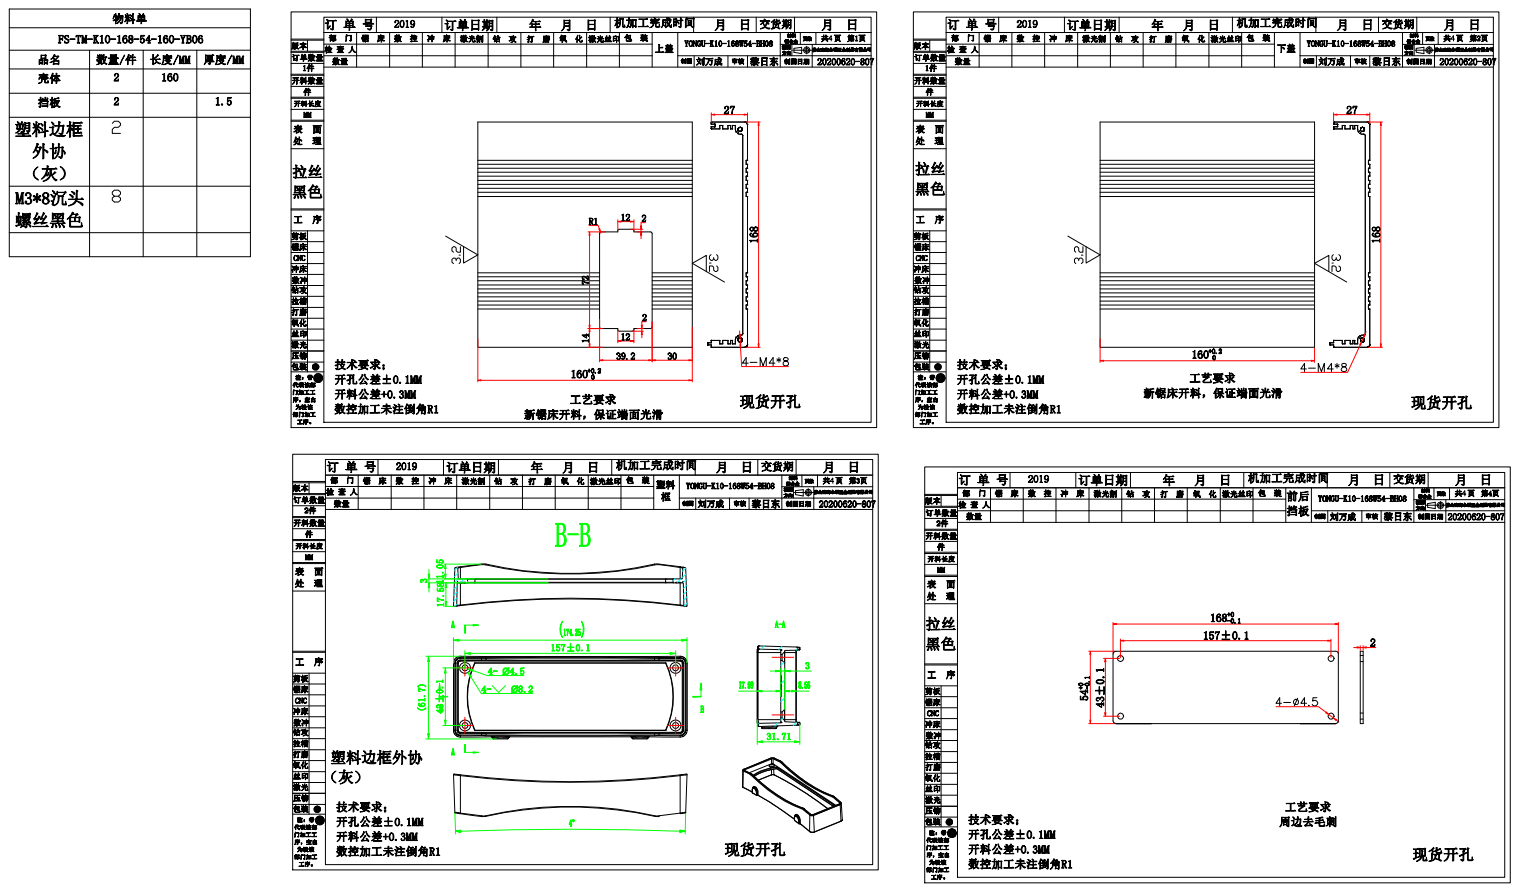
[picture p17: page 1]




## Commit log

2020-01-03 【更新】:bug:first commit
    [Main Board.PrjPcb, controller.SchDoc, main.SchDoc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]
2020-01-03 【更新】:smile:添加相关外设
    [controller.SchDoc, core.SchDoc, devices.SchDoc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]
2020-01-08 :hammer: update: circuit board of schdoc
    [Main Board.PrjPcb, core.SchDoc, devices.SchDoc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]
2020-01-08 :scroll: add:datasheet and sch of circuit design
2020-01-09 :artificial_satellite: update ： complete sch and 20% of layout
    [core.SchDoc, devices.SchDoc, power.SchDoc]
2020-01-09 :artificial_satellite: update ： complete sch and 30% of layout
    [Main Board.PrjPcb, core.SchDoc, devices.SchDoc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]
2020-01-10 :artificial_satellite: update ： complete sch and 50% of layout
    [Main Board.PrjPcb, core.SchDoc, devices.SchDoc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]
2020-01-11 :electric_plug: add : electronic speed controller(esc) from github
    [BLHeli_s-J_H_10.PrjPCB, BLHeli_s-J_H_30_BOM.xls, BlueESC.brd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]
2020-01-11 🛰 update ： complete 70% of sch and layout
    [Main Board.PrjPcb, core.SchDoc, devices.SchDoc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]
2020-01-11 🛰 update ： complete 85% of sch and layout
    [Main Board.PrjPcb, core.SchDoc, devices.SchDoc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]
2020-01-12 :tada: Release:rovmater mainboard v1.0
    [Main Board.PrjPcb, core.SchDoc, devices.SchDoc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]
2020-02-26 :hammer: Modify: sch structure
    [Main Board.PrjPcb, main.SchDoc]
2020-03-21 :book:Docs: add pca9685、ads1118 datasheet
2020-04-24 :hammer: 更改depth sensor线序、增加USB转TTL模块、变焦Camera接口
    [core.SchDoc, devices.SchDoc, main.SchDoc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]
2020-04-26 :hammer: 完善板子布线
    [Main Board.PrjPcb, devices.SchDoc, power.SchDoc]
2020-04-28 :hammer: 优化原题图布局及连接
    [core.SchDoc, devices.SchDoc, power.SchDoc]
2020-04-29 :hammer: Change: 优化完善原理图
    [Main Board.PrjPcb, core.SchDoc, devices.SchDoc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]
2020-05-05 :hammer: Change: 完善原理图布局
    [Main Board.PrjPcb, core.SchDoc, power.SchDoc]
2020-05-06 :sparkles: Add: 添加MP1584稳压电路原理图
    [MP1584.PrjPcb, MP1584.SchDoc]
2020-05-31 :sparkles: Add: 添加舱内电源板
    [Powerboard in ROV V1.0.PcbDoc, Powerboard in ROV V1.0.PcbLib, Powerboard in ROV V1.0.PrjPCB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]
2020-06-01 :hammer: update
    [Powerboard in ROV V1.0.PcbDoc]
2020-06-03 :hammer: update: 优化电源输入
    [Main Board.PrjPcb, core.SchDoc, devices.SchDoc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]
2020-06-11 :hammer: 完成PCB基本空间结构布局
    [Main Board.PrjPcb, core.SchDoc, devices.SchDoc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]
2020-06-11 :hammer: update: 完成sch，完成基本PCB布线
    [Main Board.PrjPcb, Mylib.SchLib, devices.SchDoc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]
2020-06-12 :sparkles: update: 完成PCB设计
    [Powerboard in ROV V1.0.PrjPCB, Powerboard in ROV V1.0.SchDoc]
2020-06-12 :hammer: update: 完成PCB布线及标号放置
    [Main Board.PrjPcb, MainBoard.PrjPcb, Mylib.SchLib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]
2020-06-13 :books: Add: 添加相关数据手册、规格书
2020-06-13 :sparkles: update: complete PCB degisn
    [Powerboard in ROV V1.0.PcbDoc, Powerboard in ROV V1.0.PrjPCB]
2020-06-13 :sparkles: update: complete PCB design
    [MainBoard.PrjPcb, devices.SchDoc]
2020-06-13 :white_check_mark: Add: PCB STEP 3D
    [MainBoard.PrjPcb]
2020-06-14 :memo: Add: readme
    [MainBoard.PrjPcb]
2020-06-14 :memo: update: readme
    [MP1584.PrjPcb, MP1584.SchDoc, Powerboard in ROV V1.0.PrjPCB]
2020-06-15 :hammer: Change: dir name
    [Ground Station.PrjPcb, Main Board.PrjPcb, MainBoard.PrjPcb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]
2020-06-15 :memo: update
    [BLHeli_s-J_H_10.PrjPCB, BLHeli_s-J_H_30_BOM.xls, BlueESC.brd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]
2020-06-19 :hammer: update: 地面站完成基本布局、布线
    [Ground Station.PrjPcb, core.SchDoc, device.SchDoc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]
2020-06-20 :sparkles: completed: 地面站PCB
    [Ground Station.PrjPcb, device.SchDoc, power.SchDoc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]
2020-06-20 :hammer: Change: 电源板文件夹重命名
    [Powerboard in ROV V1.0.PcbDoc, Powerboard in ROV V1.0.PrjPCB, Powerboard in ROV V1.0.SchDoc]
2020-06-21 :sparkles: update: 完成地面站侧面板开孔设计
    [device.SchDoc, 上盖板开孔尺寸图.PcbDoc, 地面站上盖板开孔尺寸图.PcbDoc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]
2020-06-22 :hammer: update: 完成变焦镜头控制板原理图
    [Zoom Camera V1.0.PcbDoc, Zoom Camera V1.0.PrjPcb, Zoom Camera V1.0.SchDoc]
2020-06-23 :sparkles: update: 完成变焦控制板设计
    [Zoom Camera Controller V1.0.PcbDoc, Zoom Camera Controller V1.0.PrjPcb, Zoom Camera Controller V1.0.SchDoc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]
2020-06-23 :memo: update: 提交电源芯片datasheet
2020-06-23 :sparkles: Add: MP1584(24V 3A VRM)
    [MP1584.PrjPcb, MP1584.SchDoc]
2020-06-27 :hammer: Fixed: 修正了光电转换器 网络不通问题
    [Ground Station.PrjPcb, device.SchDoc]
2020-06-28 :hammer: Fixed: 修正原理图标号错误
    [Zoom Camera Controller V1.0.PcbDoc, Zoom Camera Controller V1.0.PrjPcb, Zoom Camera Controller V1.0.SchDoc]
2020-06-28 :hammer: update: 新增变焦镜头 达林顿管驱动板(原因:A4988并不适用于该步进电机)
    [Zoom Camera Controller V2.0.PcbDoc, Zoom Camera Controller V2.0.PrjPcb, Zoom Camera Controller V2.0.SchDoc]
2020-06-28 :hammer: Fixed: 修正侧板定位孔竖直距离(向上1.5mm)
    [地面站侧板开孔尺寸图1.PcbDoc]
2020-06-29 :hammer: modify: 增大侧面板指示灯扣铜logo
    [地面站侧板开孔尺寸图1.PcbDoc]
2020-06-29 :book: modify: 修改datasheet存放目录
2020-06-29 :book: modify: 新增文档目录
2020-07-02 :hammer: Fixed: 添加新版本 变焦驱动控制板（修正之前版本驱动芯片不适用的情况）
    [Zoom Camera Controller V2.0.SchDoc, Zoom Camera Controller V3.0.PrjPcb, Zoom Camera Controller V3.0.SchDoc]
2020-07-06 :memo: update: datasheets
    [Rov Master 2020.6 电子器件支出明细 .xlsx]
2020-08-30 :memo: Docs: add MT7688 datasheet
    [7688A_59pin.PcbLib, 7688A原理图封装.SchLib, 7688A参考设计原理图.schdoc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]
